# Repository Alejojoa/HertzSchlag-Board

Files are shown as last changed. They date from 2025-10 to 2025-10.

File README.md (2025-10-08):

# HertzSchlag - Mini Sumo Board
The HertzSchlag is a PCB designed for Mini Sumo Robots.

Captura de pantalla 2025-10-08 182923

Captura de pantalla 2025-10-08 182933

Captura de pantalla 2025-10-08 183044

## Features :
- Dedicated Servo Pin with PWM control
- Dedicated Start Module pin

- Capability to connect up to 10 sensors (2 analog GPIO, 4 digital GPIO and 4 analog and digital GPIO)
- Mini 360 Step Down
- Two programmable buttons
- XT30 connector and JST(2.54 header pin 1x02)
- On/Off switch
- M2 mounting holes for secure mounting

## Highly Inspired By Tenn Board From DENJU DIVISION :
https://github.com/DENJU-DIVISION/Tenn-PCB/tree/main

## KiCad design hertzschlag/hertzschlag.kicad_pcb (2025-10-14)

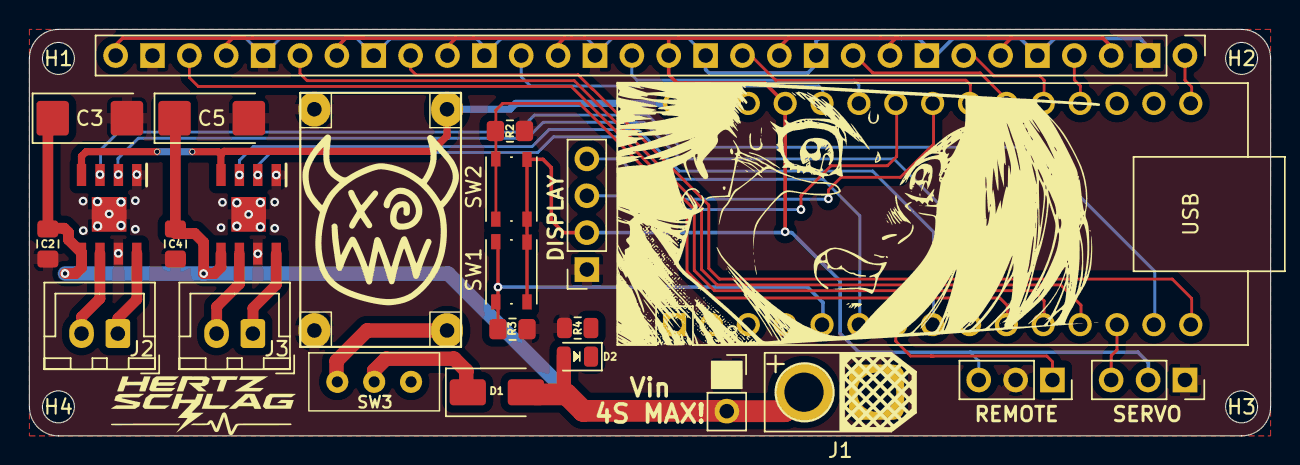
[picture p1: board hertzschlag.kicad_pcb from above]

Board: 2 copper layers, 85.5 x 28.0 mm, 28 parts (0 on the bottom side), 31 nets.

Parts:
A2: Arduino_Nano_v3.x; Arduino_Nano
C2, C4: 100nF; C_0805_2012Metric_Pad1.18x1.45mm_HandSolder
C3, C5: 47uF; CP_EIA-6032-15_Kemet-U_HandSolder
D1: M7; D_SMA
D2: LED; LED_0805_2012Metric
DISPLAY: Conn_01x04_Female; PinSocket_1x04_P2.54mm_Vertical
H1, H2, H3, H4: MountingHole; MountingHole_2.2mm_M2_ISO7380
IC1, IC2: TB67H450FNG,EL; SOIC127P600X175-9N
J1: TB_1X2; AMASS_XT30U-F_1x02_P5.0mm_Vertical
J2: MotorA; JST_XH_B2B-XH-A_1x02_P2.50mm_Vertical
J3: MotorB; JST_XH_B2B-XH-A_1x02_P2.50mm_Vertical
J4: Conn_01x30_Pin; PinHeader_1x30_P2.54mm_Vertical
J8: Extra; PinSocket_1x02_P2.54mm_Vertical
R2, R3: R; R_0805_2012Metric_Pad1.20x1.40mm_HandSolder
R4: 2.7K; R_0805_2012Metric
REMOTE: Conn_01x03_Male; PinSocket_1x03_P2.54mm_Vertical
SERVO: Conn_01x03_Male; PinSocket_1x03_P2.54mm_Vertical
SW1, SW2: SW_Push; SW_Push_1P1T_NO_Vertical_Wuerth_434133025816
SW3: SW_Push; SW_Slide-03_P2.54_L9_W4_H7
U3: Mini360; Mini360_step-down

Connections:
+5V: A2.27 (+5V), DISPLAY.2, J4.3, J4.6, J4.9, J4.12, J4.15, J4.18, J4.21, J4.24, J4.27, J4.30, REMOTE.3, SERVO.2, SW1.2, SW2.2
/BTN1: A2.5 (D2), R3.2, SW1.1
/BTN2: A2.10 (D7), R2.2, SW2.1
/IN_A1: A2.14 (D11), IC1.3 (IN1)
/IN_A2: A2.9 (D6), IC1.2 (IN2)
/IN_B1: A2.8 (D5), IC2.3 (IN1)
/IN_B2: A2.6 (D3), IC2.2 (IN2)
/MSJS: A2.7 (D4), REMOTE.1
/OUT_A1: IC1.6 (OUT1), J2.2
/OUT_A2: IC1.8 (OUT2), J2.1
/OUT_B1: IC2.6 (OUT1), J3.2
/OUT_B2: IC2.8 (OUT2), J3.1
/SCL: A2.24 (A5), DISPLAY.3
/SDA: A2.23 (A4), DISPLAY.4
/SENSOR0: A2.11 (D8), J4.28
/SENSOR1: A2.12 (D9), J4.25
/SENSOR2: A2.15 (D12), J4.22
/SENSOR3: A2.16 (D13), J4.1
/SENSOR4: A2.19 (A0), J4.4
/SENSOR5: A2.20 (A1), J4.7
/SENSOR6: A2.21 (A2), J4.10
/SENSOR7: A2.22 (A3), J4.13
/SENSOR8: A2.25 (A6), J4.16
/SENSOR9: A2.26 (A7), J4.19
/Servo: A2.13 (D10), SERVO.3
/VM: C2.1, C3.1, C4.1, C5.1, D1.2 (A), D2.2 (A), IC1.5 (VM), IC2.5 (VM), J1.2, J8.2
GND: A2.4 (GND), A2.29 (GND), C2.2, C3.2, C4.2, C5.2, DISPLAY.1, IC1.1 (GND), IC1.7 (RS), IC1.9 (EP), IC2.1 (GND), IC2.7 (RS), IC2.9 (EP), J1.1, J4.2, J4.5, J4.8, J4.11, J4.14, J4.17, J4.20, J4.23, J4.26, J4.29, J8.1, R2.1, R3.1, R4.2, REMOTE.2, SERVO.1, U3.2 (GND)
unnamed: D1.1 (K), SW3.2
unnamed: D2.1 (K), R4.1
unnamed: SW3.1, U3.1 (IN)
VCC: A2.30 (VIN), IC1.4 (VREF), IC2.4 (VREF), U3.3 (OUT)

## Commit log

2025-09-12 Changes on PCB.
    Changes to Footprints, Routing, Alignment.
    And no more falling alita on the front Silk screen (sad).
    [hertzschlag.kicad_pcb, hertzschlag.kicad_sch]
2025-10-05 Updated PCB design
    Changes to XT30 Connector and routing.
    [hertzschlag.kicad_pcb]
2025-10-05 Added PCB directory again
    [hertzschlag.kicad_pcb, hertzschlag.kicad_sch]
2025-10-05 PCBWAY files
    [hertzschlag.kicad_pcb_bom.csv, hertzschlag.kicad_pcb_positions.csv]
2025-10-08 Delete hertzschlag/pcbway_production/2025-10-05-16-16-27 directory
    Old Files
    [hertzschlag.kicad_pcb_bom.csv, hertzschlag.kicad_pcb_positions.csv]
2025-10-08 Delete hertzschlag directory
    OLD FILES
    [hertzschlag.kicad_pcb, hertzschlag.kicad_sch]
2025-10-08 PCB and PCBWAY FILES
    Added Last PCB Changes and PCBWAY fabrication files
    [hertzschlag.kicad_pcb, hertzschlag.kicad_sch]
2025-10-14 PCB and production
    [hertzschlag.kicad_pcb]
